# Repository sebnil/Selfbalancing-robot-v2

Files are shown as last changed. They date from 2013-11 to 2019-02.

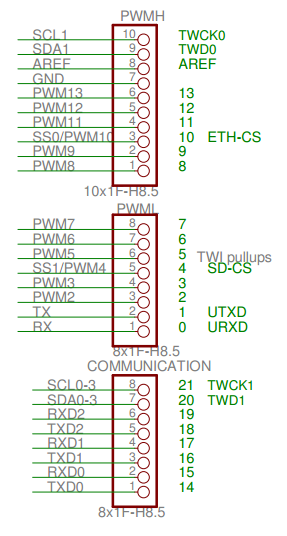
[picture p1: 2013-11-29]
schematics/Altium Designer project/arduino pins2.png

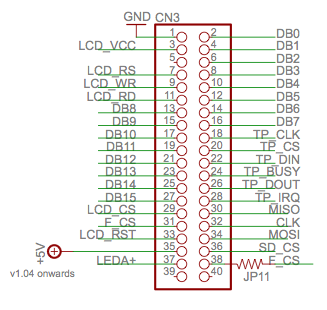
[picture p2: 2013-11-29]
schematics/Altium Designer project/lcd_pins.png

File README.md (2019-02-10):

# Selfbalancing-robot-v2

Selfbalancing robot with Arduino Due. For more details http://sebastiannilsson.com/en/k/projekt/selfbalancing-robot/

## Video
<a href="http://www.youtube.com/watch?feature=player_embedded&v=WN2oXuavrWk
" target="_blank">Selfbalancing robot</a>

## Support my creation of open source software:


<a href='https://ko-fi.com/A0A2HYRH' target='_blank'>Buy Me a Coffee at ko-fi.com</a>

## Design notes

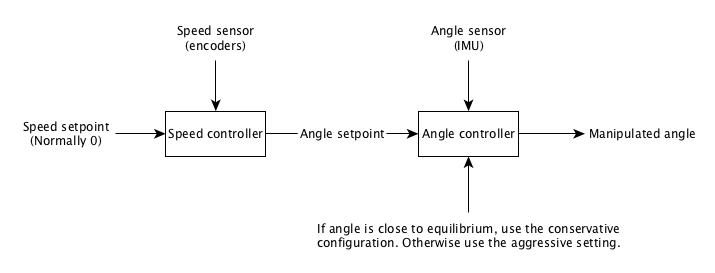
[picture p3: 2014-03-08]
Control theory/Information flow.png

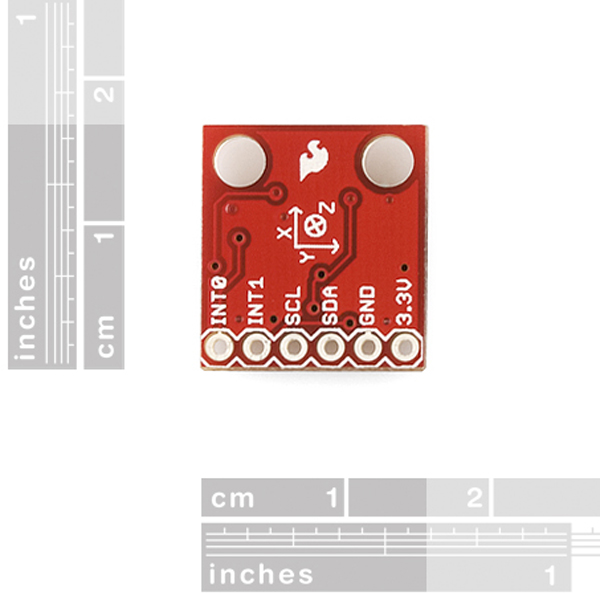
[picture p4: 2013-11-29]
schematics/Altium Designer project/sparkfun 6DOF.jpeg

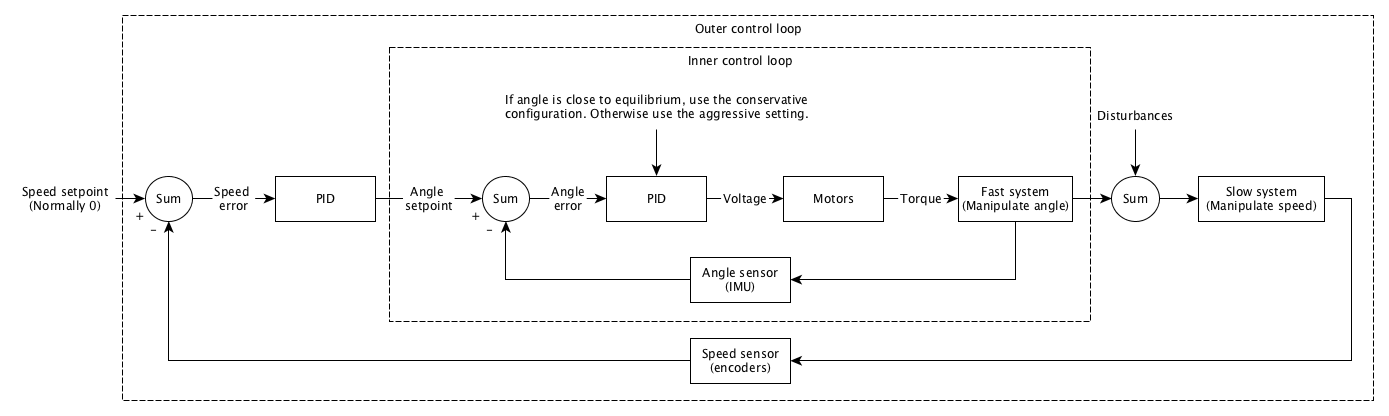
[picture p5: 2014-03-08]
Control theory/Cascade PID implementation theory.png

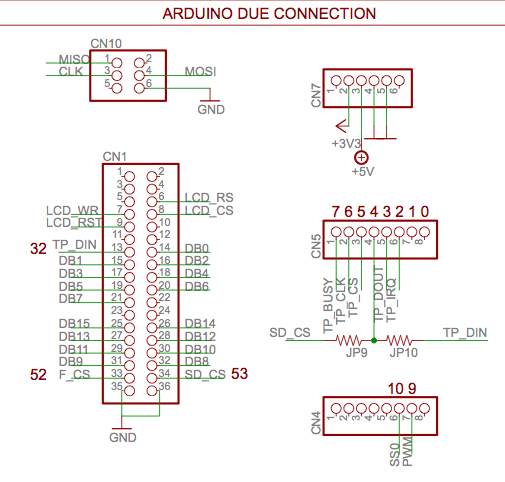
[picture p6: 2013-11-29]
schematics/Altium Designer project/lcd_arduino_connection.png

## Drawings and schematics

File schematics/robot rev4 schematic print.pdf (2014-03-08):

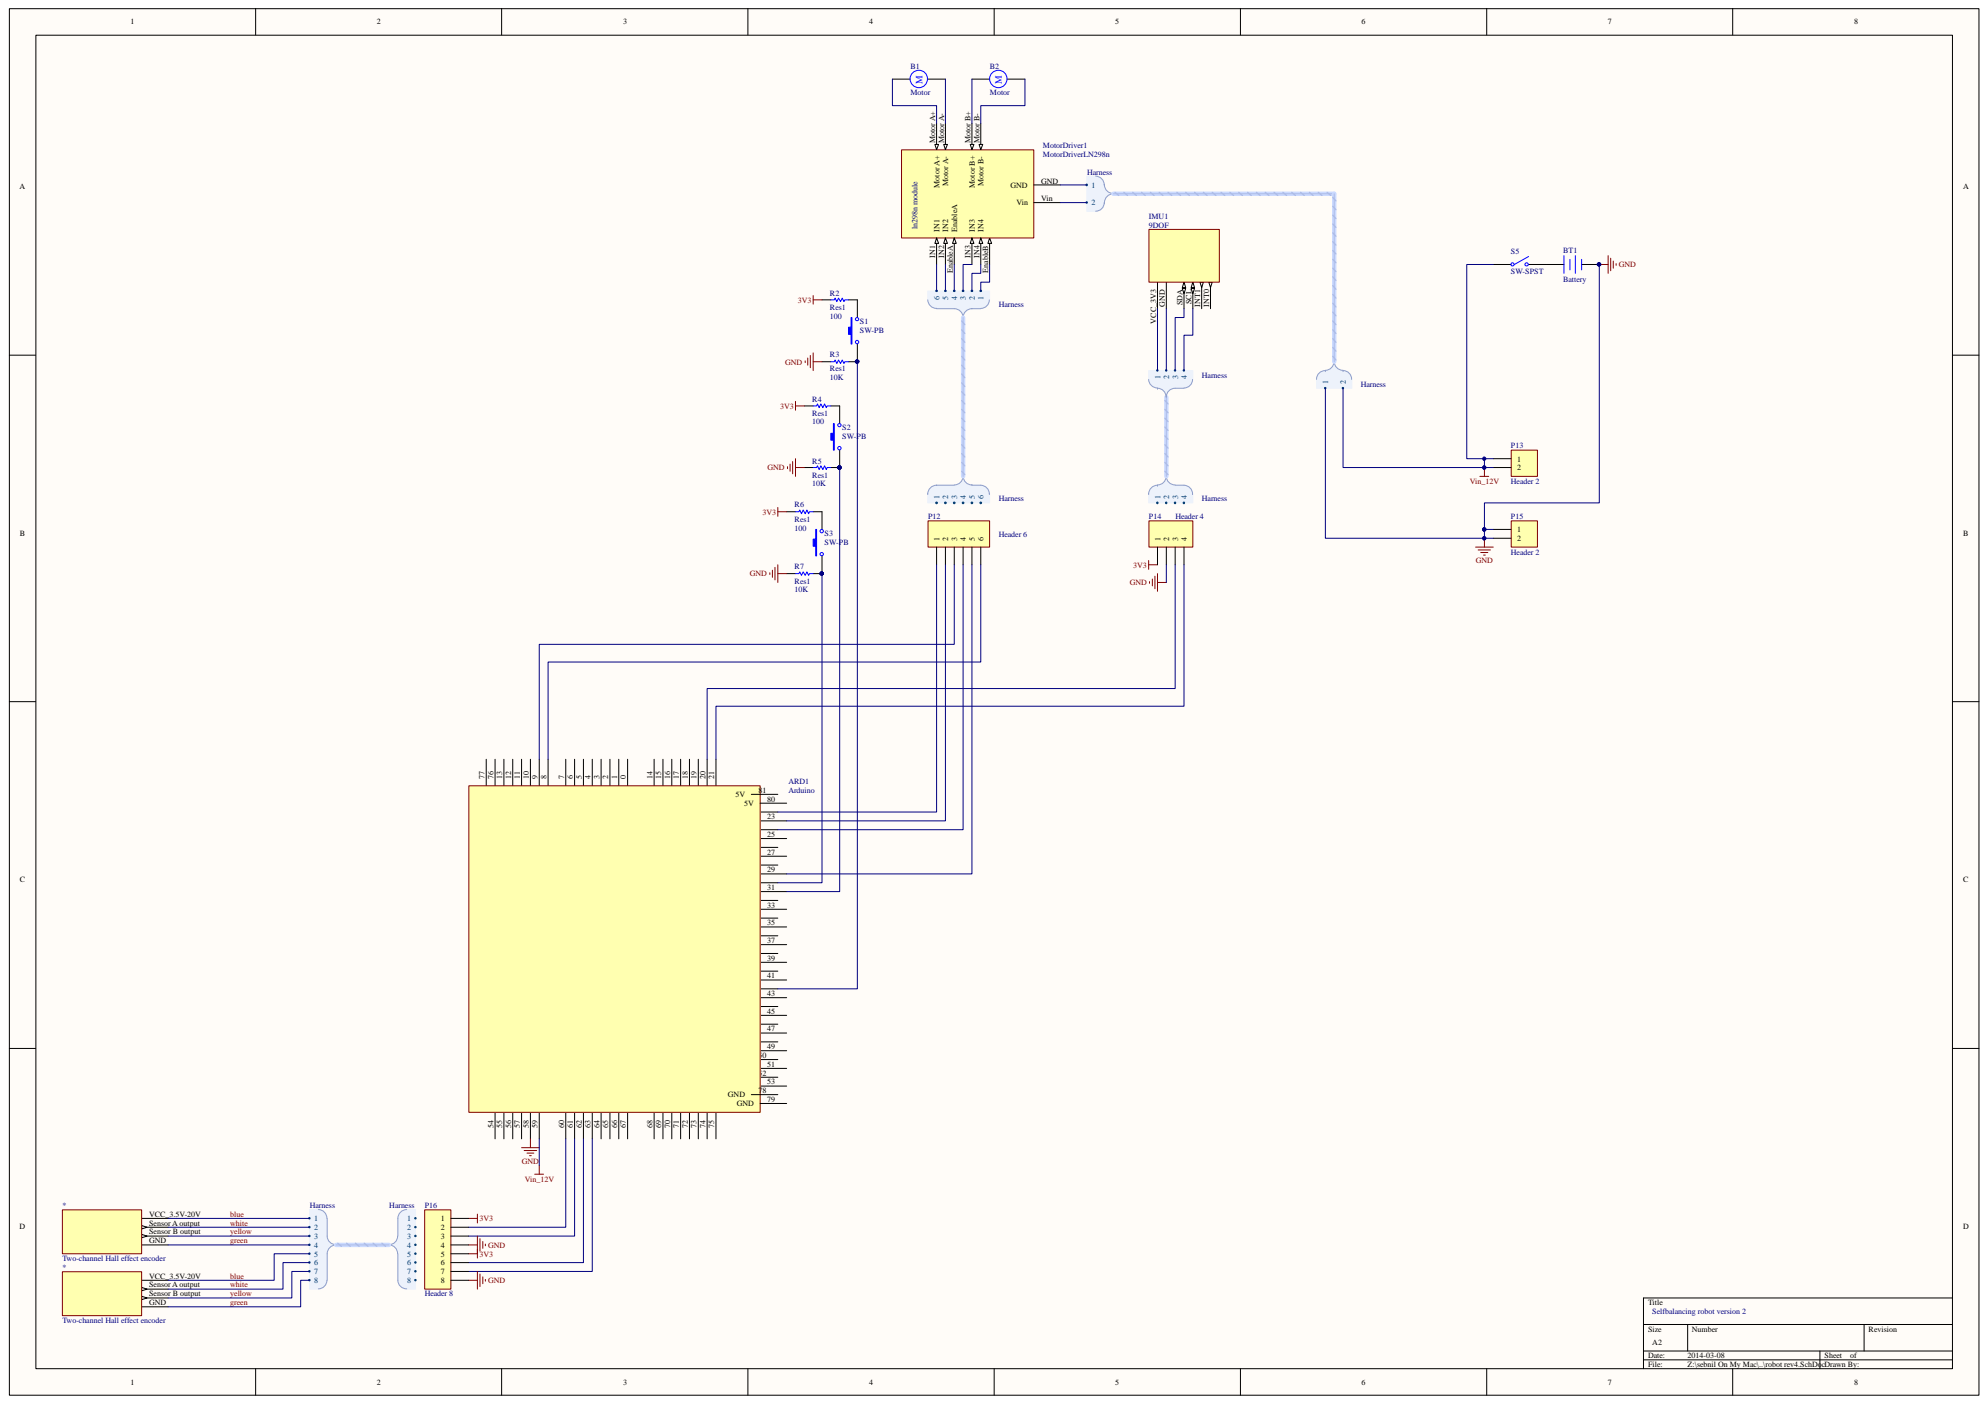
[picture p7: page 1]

Two-channel Hall effect encoder

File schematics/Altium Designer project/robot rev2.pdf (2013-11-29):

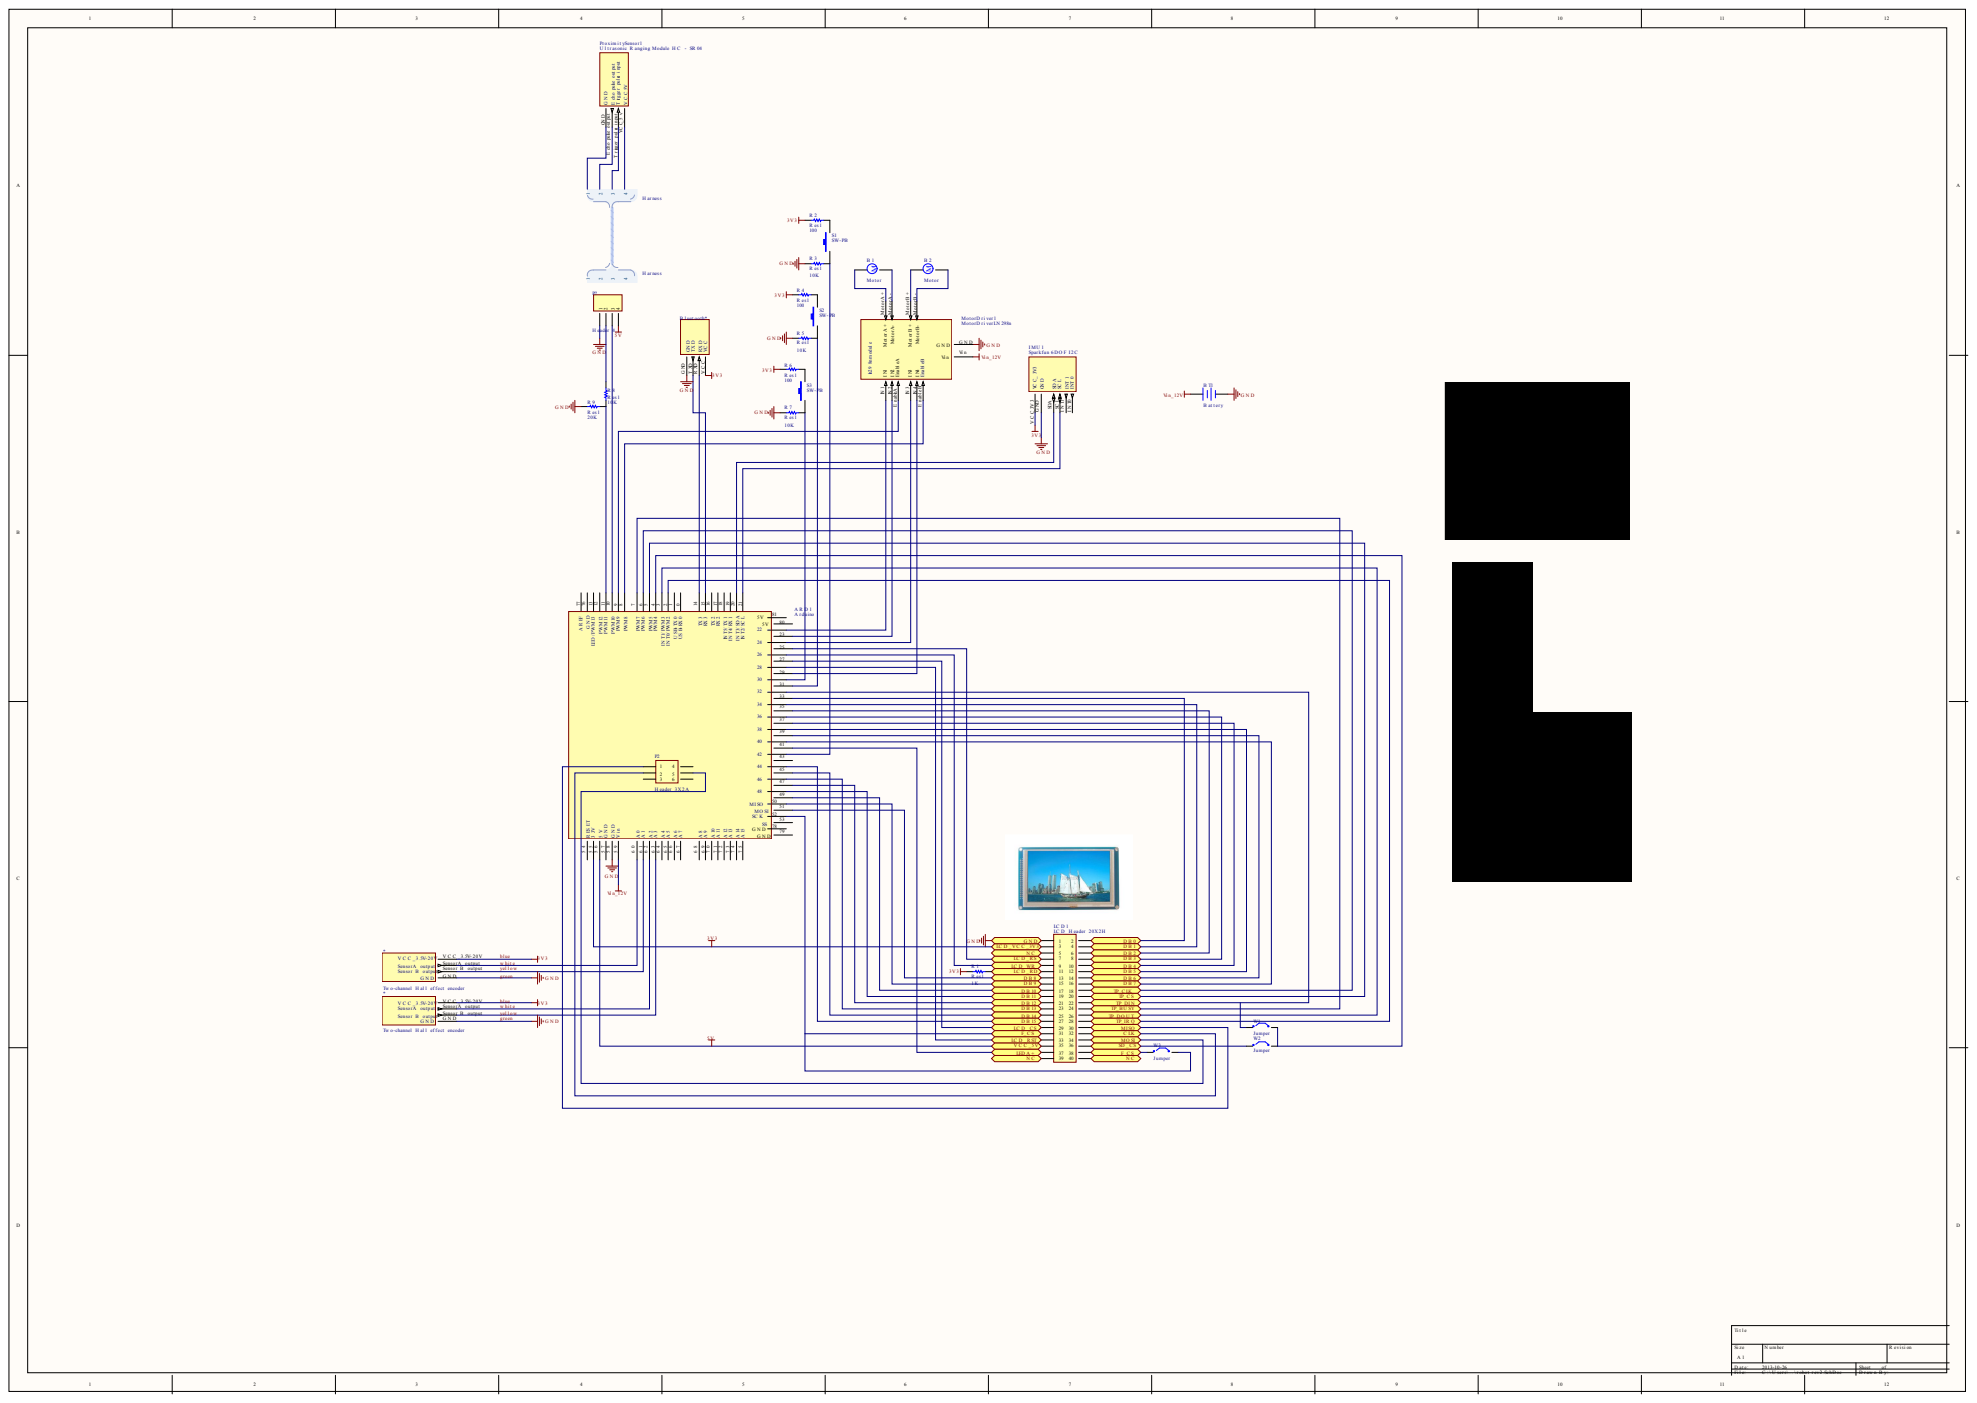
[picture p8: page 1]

Pr oxim i t ySensor1
U l t r asonic R anging Module H C - SR 04

VC C_5 v T ri gger pul se i nput T r igger pul se i nput E cho pulse out put

E cho puls e out put G N D GN D

Mot or A +

Mot or A- Mot or A -

Mot or B +

Mot or B- Mot or B -

Enabl eA E nableA I N2 IN 2

Enabl eB E nabl eB I N4 IN 4

A r duino

blue 3V3 | Vi n_12V | 3V3

SensorA output Sensor B output Sensor | SensorA output | w hit e B output yel l ow | R 1 | LC D _RS LC D _WR LC D _R D | 7 9 11 12 10 | 8 D B 3 D B 4 D B 5

Tw o-channel H al l ef f ect encoder

green blue | 3V3 | R es1 3V3 1K | D B 8 D B 9 | 13 14 15 16 | D B 6 D B 7

LC D _RST | 33 34 | MO SI

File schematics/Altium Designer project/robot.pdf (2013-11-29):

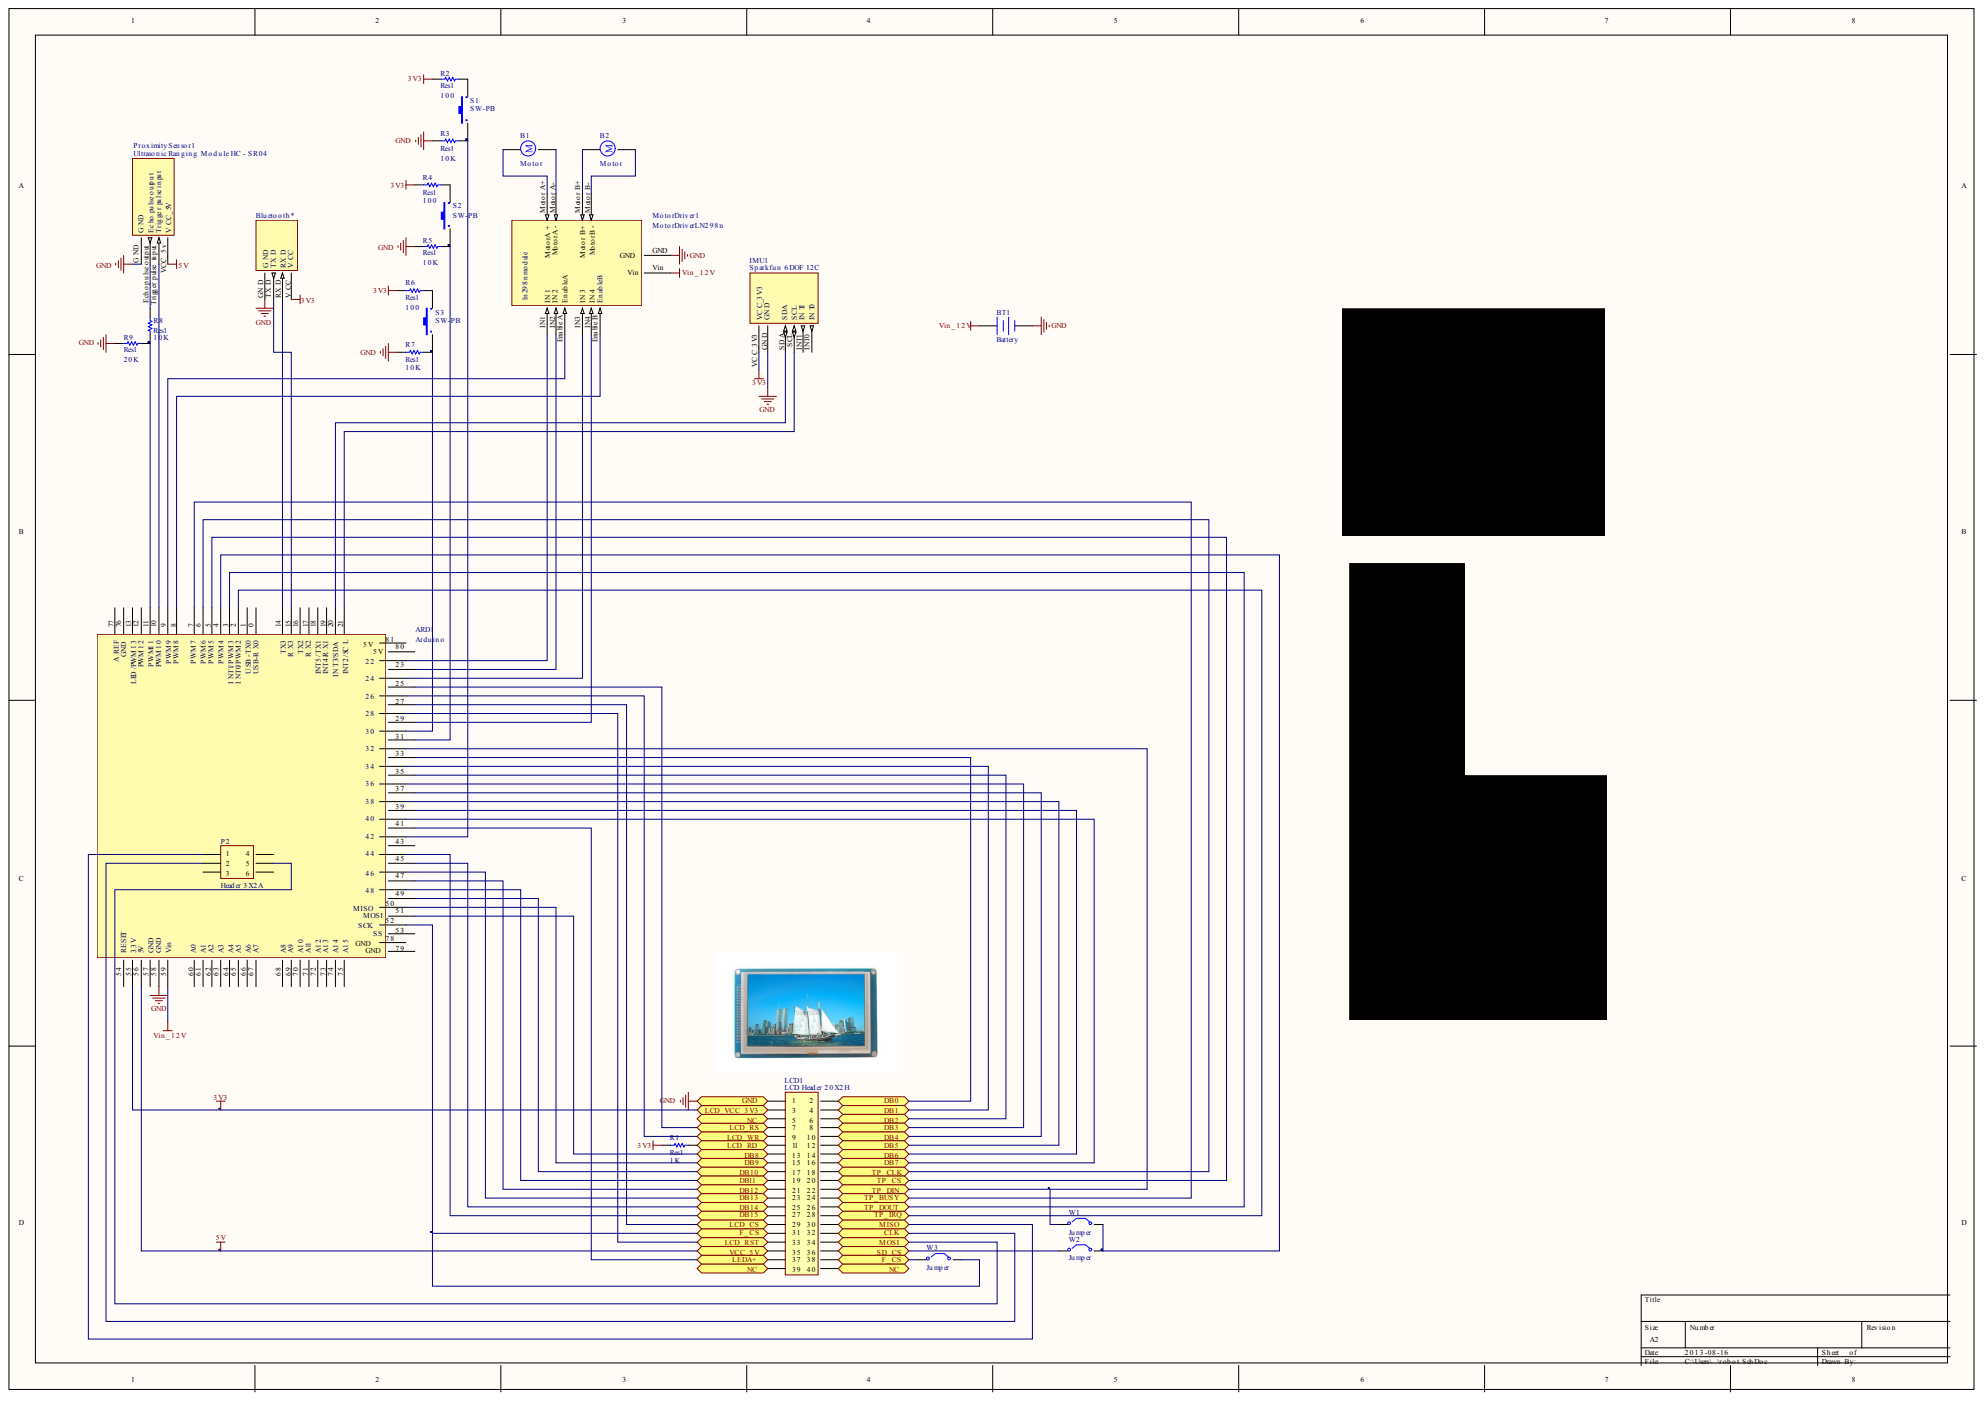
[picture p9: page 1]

V CC_ 5V VCC_ 5 v Trig ge r pu lse in pu t Trigg er p ulse in p ut Ec ho pu lse o u tp u t Ech o p u lse o utp ut G ND G ND Prox imity Sen so r1 Ultraso n ic Ran g in g Mo d u le HC - SR04

Mo to rA - Moto r A- Moto rA + Moto r A+

Mo to rB - Moto r B- Moto r B+ Moto r B+

En ab leA Ena ble A IN 2 IN2 IN 1 IN1

En ab leB Ena ble B IN 4 IN4 IN 3 IN3

IN T0 INT0 IN T1 INT1 SCL SCL SDA SD A

Res1 1 0 K

LCD_ VCC_3 V3 | 3 4

NC | 5 6 | DB2
LCD_RS | 7 8

3 V3 Res1 | DB8

R1 | LCD_ WR LCD_RD | 9 1 0 11 1 2

DB10 DB11 | 1 7 1 8 1 9 2 0 | TP_CLK TP_CS

DB12 DB13 | 2 1 2 2 2 3 2 4 | TP_ DIN TP_BUSY

DB14 | 2 5 2 6 | TP_ DOUT
DB15 | 2 7 2 8 | | W1

LCD_CS F_CS | 2 9 3 0 3 1 3 2

LCD_RST | 3 3 3 4 | MOSI W3

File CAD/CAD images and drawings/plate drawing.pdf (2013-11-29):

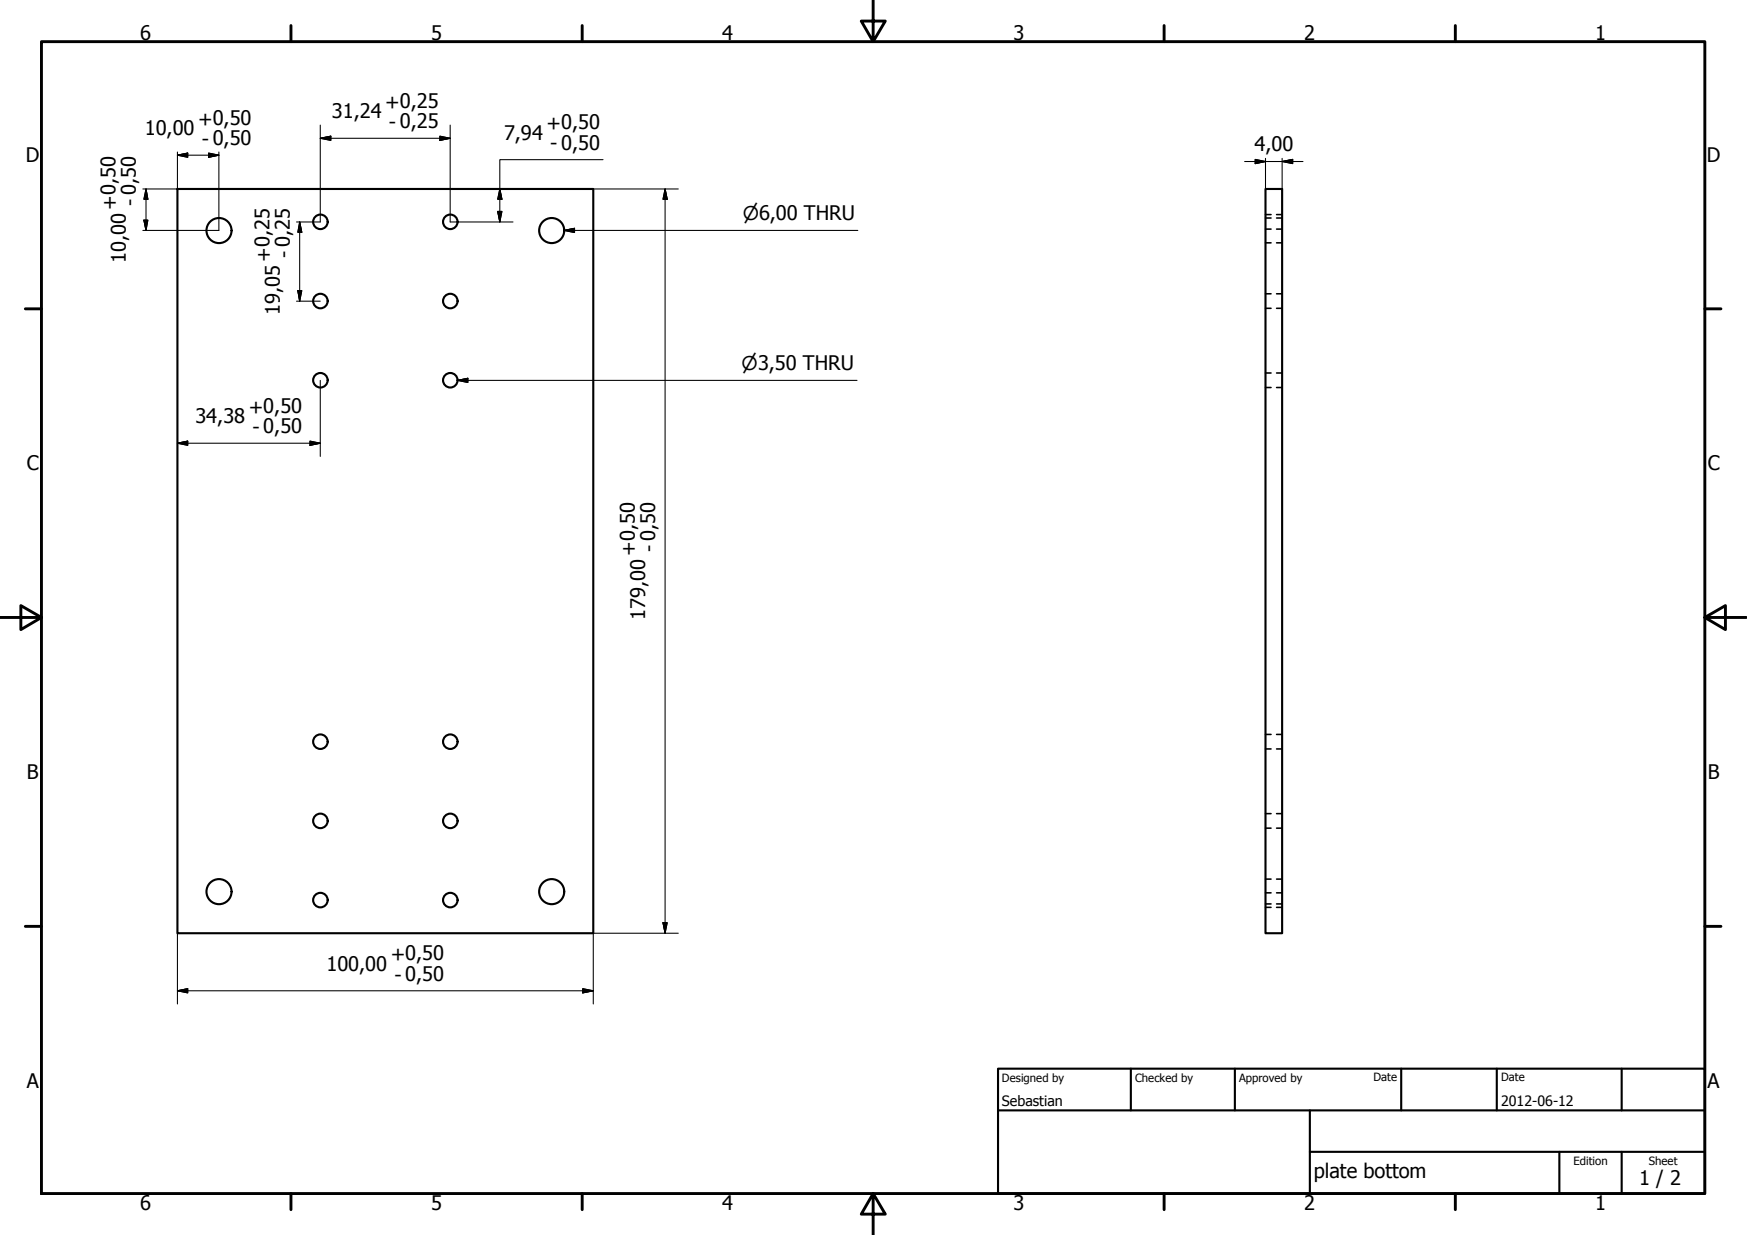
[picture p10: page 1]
plate bottom; Sebastian; Designed by; Checked by; Approved by; Date; Edition; Sheet; P3,50 THRU; P6,00 THRU

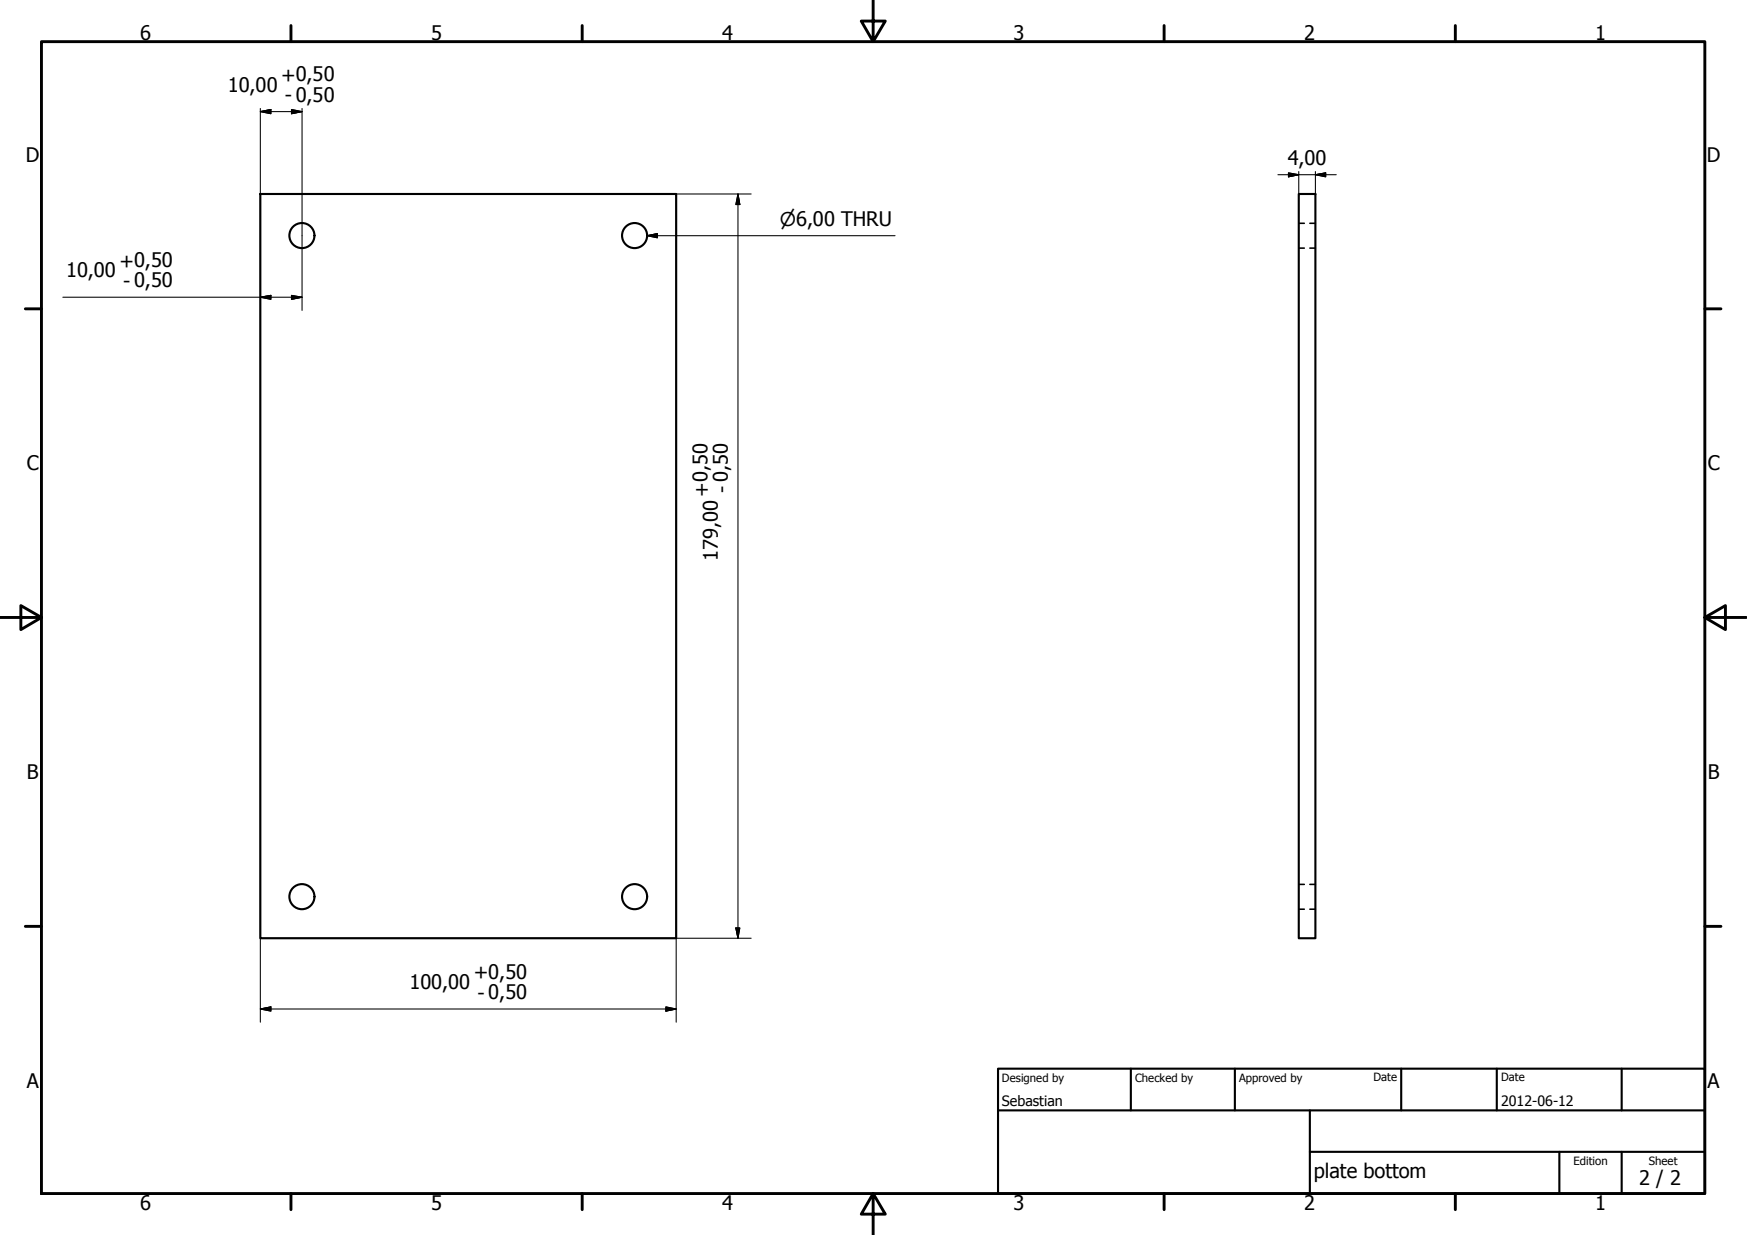
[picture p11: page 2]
plate bottom; Sebastian; Designed by; Checked by; Approved by; Date; Edition; Sheet; P6,00 THRU

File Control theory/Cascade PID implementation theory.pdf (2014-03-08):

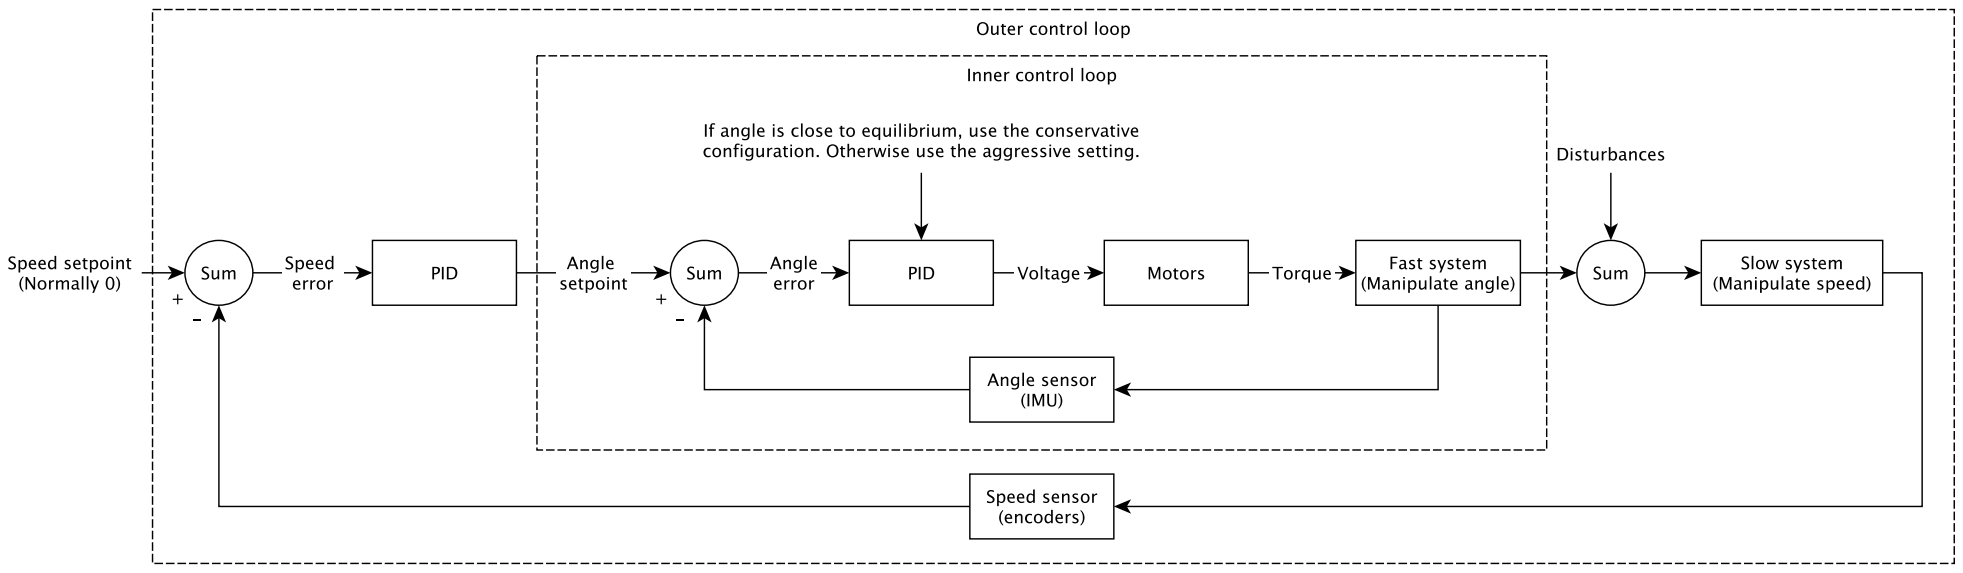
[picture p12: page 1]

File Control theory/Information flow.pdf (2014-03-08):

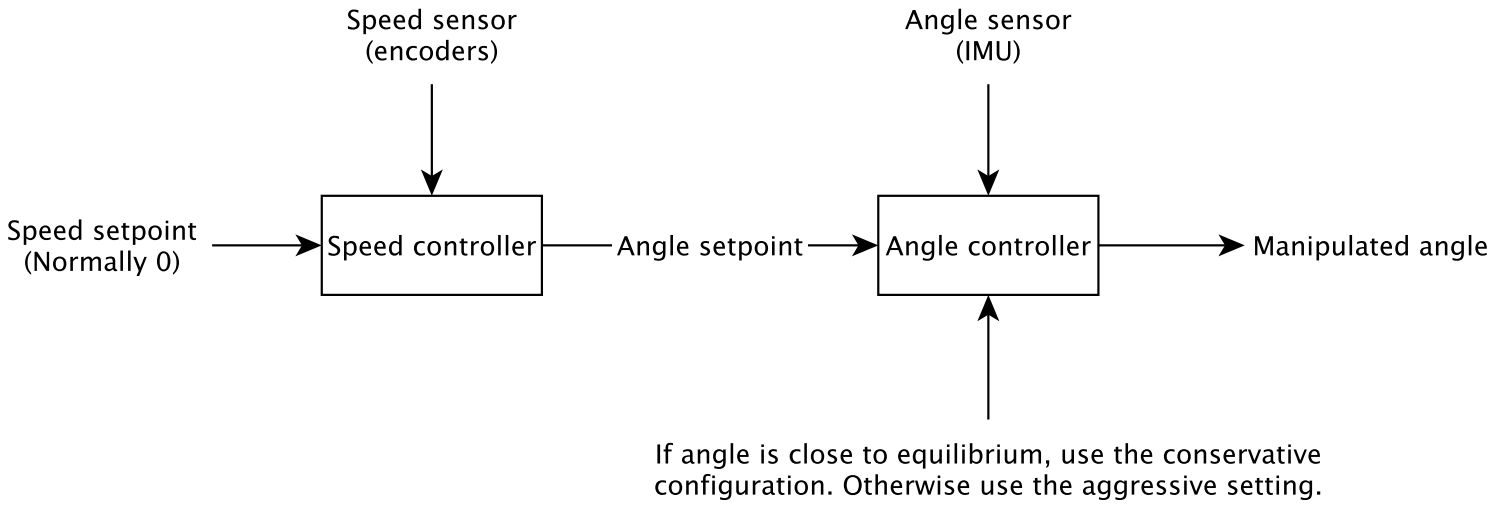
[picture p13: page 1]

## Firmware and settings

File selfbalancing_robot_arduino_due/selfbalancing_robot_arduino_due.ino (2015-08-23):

#include <Wire.h>
#include <stdlib.h>
#include <L29x.h> //https://github.com/sebnil/L29x
#include <PID_v1.h> //github.com/mwoodward/Arduino-PID-Library
#include <Button.h>        //github.com/JChristensen/Button
#include <SerialCommand.h> //github.com/kroimon/Arduino-SerialCommand
#include <MovingAvarageFilter.h> //github.com/sebnil/Moving-Avarage-Filter--Arduino-Library-
//#include <FIR.h> // github.com/sebnil/FIR-filter-Arduino-Library
#include <FIR_v2.h> // https://github.com/sebnil/FIR_v2
#include <KalmanFilter.h> // https://github.com/sebnil/KalmanFilter-for-Arduino
#include <FreeRTOS_ARM.h> //https://github.com/greiman/FreeRTOS-Arduino
#include <DueFlashStorage.h> //https://github.com/sebnil/DueFlashStorage

DueFlashStorage dueFlashStorage;


// Redefine AVR Flash string macro as nop for ARM
#undef F
#define F(str) str

#define TO_RAD(x) (x * 0.01745329252)  // *pi/180
#define TO_DEG(x) (x * 57.2957795131)  // *180/pi

const uint8_t LED_PIN = 13;

// motor config
#include <L29x.h>
L29x motorLeft(9, 22, 23); // enable (PWM), motor pin 1, motor pin 2
L29x motorRight(8, 24, 29); // enable (PWM), motor pin 1, motor pin 2

// button declarations
Button startBtn(30, false, false, 20);
Button stopBtn(31, false, false, 20);
Button calibrateBtn(42, false, false, 20);

// start and stop
boolean started = true;

SerialCommand sCmd;     // The demo SerialCommand object

// PID variables
double anglePIDSetpoint, anglePIDInput, anglePIDOutput;
double speedPIDInput, speedPIDOutput, speedPIDSetpoint;
double anglePIDInputFiltered;

// filters
MovingAvarageFilter speedMovingAvarageFilter(14);
MovingAvarageFilter angleMovingAvarageFilter(4);
KalmanFilter speedKalmanFilter;
KalmanFilter angleKalmanFilter;
FIR_v2 speedMovingAvarageFilter2;

// The cascading PIDs. The tunings are updated from the code
PID anglePID(&anglePIDInput, &anglePIDOutput, &anglePIDSetpoint, 0, 0, 0, DIRECT);
PID speedPID(&speedPIDInput, &speedPIDOutput, &speedPIDSetpoint, 0, 0, 0, DIRECT);

// handle for blink task
//xTaskHandle blink;

//v_read_imu_task
// Euler angles
float yaw;
float pitch;
float roll;
float angleRaw;
float roll_filtered;
// DCM timing in the main loop
unsigned long timestamp;
unsigned long timestamp_old;
float G_Dt; // Integration time for DCM algorithm

long leftMotorPosition  = 0;
long rightMotorPosition  = 0;
long lastLeftMotorPosition  = 0;
long lastRightMotorPosition  = 0;
float leftMotorSpeed  = 0;
float rightMotorSpeed  = 0;
float speedKalmanFiltered = 0;
float speedFIRFiltered = 0;

struct Configuration {
	double speedPIDKp;
	double speedPIDKi;
	double speedPIDKd;
	double speedPIDOutputLowerLimit;
	double speedPIDOutputHigherLimit;
	double anglePIDAggKp;
	double anglePIDAggKi;
	double anglePIDAggKd;
	double anglePIDConKp;
	double anglePIDConKi;
	double anglePIDConKd;
	double anglePIDLowerLimit;
	double calibratedZeroAngle;
	uint8_t anglePIDSampling;
	double angleKalmanFilterR;
	uint8_t speedPIDSampling;
	uint8_t angleSensorSampling;
	uint8_t motorSpeedSensorSampling;
	double speedKalmanFilterR;
	uint8_t motorLeftMinimumSpeed;
	uint8_t motorRightMinimumSpeed;
	uint8_t debugLevel;
	uint8_t debugSampleRate;
	uint8_t speedPIDOutputDebug;
	uint8_t speedPIDInputDebug;
	uint8_t speedKalmanFilterDebug;
	uint8_t speedRawDebug;
	uint8_t speedMovingAvarageFilter2Debug;
	uint8_t anglePIDSetpointDebug;
	uint8_t anglePIDInputDebug;
	uint8_t anglePIDOutputDebug;
	uint8_t angleRawDebug;
	uint8_t  activePIDTuningDebug;
};
Configuration configuration;
byte b[sizeof(Configuration)];

struct UserControl {
	float steering;
	float direction;
};
UserControl userControl = {0, 0};


void setConfiguration() {
	/* Flash is erased every time new code is uploaded. Write the default configuration to flash if first time */
	// running for the first time?
	uint8_t codeRunningForTheFirstTime = dueFlashStorage.read(0); // flash bytes will be 255 at first run
	if (codeRunningForTheFirstTime) {
		Serial.println("codeRunningForTheFirstTime");
		/* OK first time running, set defaults */
		configuration.speedPIDKp = 0.85;
		configuration.speedPIDKi = 0.10;
		configuration.speedPIDKd = 0.00;
		configuration.speedPIDOutputLowerLimit = -10.00;
		configuration.speedPIDOutputHigherLimit = 10.00;
		configuration.anglePIDAggKp = 20.00;
		configuration.anglePIDAggKi = 0.20;
		configuration.anglePIDAggKd = 0.70;
		configuration.anglePIDConKp = 15.00;
		configuration.anglePIDConKi = 0.00;
		configuration.anglePIDConKd = 0.25;
		configuration.anglePIDLowerLimit = 5.00;
		configuration.calibratedZeroAngle = -10.87;
		configuration.anglePIDSampling = 10;
		configuration.speedPIDSampling = 15;
		configuration.angleKalmanFilterR = 10.00;
		configuration.angleSensorSampling = 5;
		configuration.motorSpeedSensorSampling = 5;
		configuration.speedKalmanFilterR = 20.00;
		configuration.motorLeftMinimumSpeed = 55;
		configuration.motorRightMinimumSpeed = 55;
		
		configuration.debugLevel = 0;
		configuration.debugSampleRate = 50;
		//  configuration.speedPIDSetpointDebug = 1;
		configuration.speedPIDOutputDebug = 1;
		configuration.speedPIDInputDebug = 1;
		configuration.speedKalmanFilterDebug = 1;
		configuration.speedRawDebug = 1;
		configuration.speedMovingAvarageFilter2Debug = 0;
		configuration.anglePIDSetpointDebug = 1;
		configuration.anglePIDInputDebug = 1;
		configuration.anglePIDOutputDebug = 1;
		configuration.angleRawDebug = 1;
		configuration.activePIDTuningDebug = 1;

		// write configuration struct to flash at address 4
		//byte b2[sizeof(Configuration)]; // create byte array to store the struct
		memcpy(b, &configuration, sizeof(Configuration)); // copy the struct to the byte array
		dueFlashStorage.write(4, b, sizeof(Configuration)); // write byte array to flash
		
		// write 0 to address 0 to indicate that it is not the first time running anymore
		dueFlashStorage.write(0, 0);
	}
	else {
		Serial.println("read configuration struct from flash");
		/* read configuration struct from flash */
		byte* b2 = (dueFlashStorage.readAddress(4)); // byte array which is read from flash at address 4
		memcpy(&configuration, b2, sizeof(Configuration)); // copy byte array to temporary struct
	}
}

void setup() {
	Serial.begin(115200);
	//  Serial3.begin(9600);
	// wait for Leonardo
	while(!Serial) {
	}
	Wire.begin();

	pinMode(A0, INPUT);
	pinMode(A1, INPUT);
	pinMode(A2, INPUT);
	pinMode(A3, INPUT);
	pinMode(30, INPUT);
	pinMode(31, INPUT);
	pinMode(42, INPUT);

	attachInterrupt(A2, A2interruptFun, RISING);
	attachInterrupt(A3, A3interruptFun, RISING);

	// filters
	speedKalmanFilter.setState(0);
	float coefficients[] = {
	1,1,1,1,1,1,1,1,1          };
	speedMovingAvarageFilter2.setCoefficients(coefficients);
	speedMovingAvarageFilter2.setNumberOfTaps(9);
	speedMovingAvarageFilter2.setGain((float) (1/9));


	setConfiguration();

	// create read imu task
	//xTaskCreate(vReadIMUTask, NULL, configMINIMAL_STACK_SIZE + 50, NULL, 1, NULL);

	// create control task
	xTaskCreate(vControlTask, NULL, configMINIMAL_STACK_SIZE + 100, NULL, 1, NULL);

	// create button task
	xTaskCreate(vInterfaceAndDebugTask,NULL, configMINIMAL_STACK_SIZE+100, NULL,1,NULL);


	// start FreeRTOS
	vTaskStartScheduler();

	// should never return
	Serial.println(F("Die"));
	while(1);
}

// WARNING idle loop has a very small stack (configMINIMAL_STACK_SIZE)
// loop must never block
volatile uint32_t count = 0;
void loop() {
	while(1) {
		// must insure increment is atomic
		// in case of context switch for print
		noInterrupts();
		count++;
		interrupts();
	}
}



void newConfig() {
	// init speed PID
	speedPIDSetpoint = 0;
	speedPID.SetOutputLimits(configuration.speedPIDOutputLowerLimit, configuration.speedPIDOutputHigherLimit);
	//anglePID.SetMode(AUTOMATIC);
	speedPID.SetSampleTime(configuration.speedPIDSampling);
	speedPID.SetTunings(configuration.speedPIDKp, configuration.speedPIDKi, configuration.speedPIDKd);

	//init angle PID
	anglePIDSetpoint = 0;
	anglePID.SetOutputLimits(-100, 100);
	//anglePID.SetMode(AUTOMATIC);
	anglePID.SetSampleTime(configuration.anglePIDSampling);
	
	angleKalmanFilter.setR(configuration.angleKalmanFilterR);
	speedKalmanFilter.setR(configuration.speedKalmanFilterR);
	
	// init motors
	motorLeft.setMinimumSpeed(configuration.motorLeftMinimumSpeed);
	motorRight.setMinimumSpeed(configuration.motorRightMinimumSpeed);
	
	// write configuration struct to flash at address 4
	//byte b2[sizeof(Configuration)]; // create byte array to store the struct
	memcpy(b, &configuration, sizeof(Configuration)); // copy the struct to the byte array
	dueFlashStorage.write(4, b, sizeof(Configuration)); // write byte array to flash
}

/* interrupt functions for counting revolutions in the encoders */
void A2interruptFun() {
	if (digitalRead(A1))
	rightMotorPosition++;
	else
	rightMotorPosition--;
}
void A3interruptFun() {
	if (digitalRead(A0))
	leftMotorPosition++;
	else
	leftMotorPosition--;
}

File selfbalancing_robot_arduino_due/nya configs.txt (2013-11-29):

speedPIDKi = 5.00;
speedPIDKd = 0.00;
anglePIDAggKp = 50.00;
anglePIDAggKi = 0.00;
anglePIDAggKd = 0.00;
anglePIDConKp = 40.00;
anglePIDConKi = 1.00;
anglePIDConKd = 0.00;
anglePIDLowerLimit = 8.00;
calibratedZeroAngle = -8.60;
anglePIDSampling = 10;
speedPIDSampling = 0;
angleSensorSampling = 10;
motorSpeedSensorSampling = 10;



2013-11-29
Configuration
configuration.speedPIDKp = 0.50;
configuration.speedPIDKi = 0.01;
configuration.speedPIDKd = 0.02;
configuration.speedPIDOutputLowerLimit = -3.00;
configuration.speedPIDOutputHigherLimit = 3.00;
configuration.anglePIDAggKp = 0.80;
configuration.anglePIDAggKi = 0.00;
configuration.anglePIDAggKd = 0.00;
configuration.anglePIDConKp = 20.00;
configuration.anglePIDConKi = 0.50;
configuration.anglePIDConKd = 0.25;
configuration.anglePIDLowerLimit = 20.00;
configuration.calibratedZeroAngle = -11.35;
configuration.anglePIDSampling = 10;
configuration.speedPIDSampling = 5;
configuration.angleSensorSampling = 10;
configuration.motorSpeedSensorSampling = 10;
configuration.debugLevel = 0;



configuration.speedPIDKp = 0.50;
configuration.speedPIDKi = 0.01;
configuration.speedPIDKd = 0.01;
configuration.speedPIDOutputLowerLimit = -3.00;
configuration.speedPIDOutputHigherLimit = 3.00;
configuration.anglePIDAggKp = 50.00;
configuration.anglePIDAggKi = 0.00;
configuration.anglePIDAggKd = 0.00;
configuration.anglePIDConKp = 20.00;
configuration.anglePIDConKi = 0.50;
configuration.anglePIDConKd = 0.25;
configuration.anglePIDLowerLimit = 5.00;
configuration.calibratedZeroAngle = -11.35;
configuration.anglePIDSampling = 10;
configuration.speedPIDSampling = 5;
configuration.angleKalmanFilterR = 1.00;
configuration.angleSensorSampling = 15;
configuration.motorSpeedSensorSampling = 10;
configuration.speedKalmanFilterR = 3.00;

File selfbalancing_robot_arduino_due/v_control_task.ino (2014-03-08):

enum PIDTuning {CONSERVATIVE, AGGRESSIVE};
PIDTuning activePIDTuning = CONSERVATIVE;

//uint32_t controlTaskTimestamp = 0;
static void vControlTask(void *pvParameters) {
	newConfig();
	
	// Init sensors
	vTaskDelay(50);  // Give sensors enough time to start
	I2C_Init();
	Accel_Init();
	Magn_Init();
	Gyro_Init();
	// Read sensors, init DCM algorithm
	vTaskDelay(20);  // Give sensors enough time to collect data
	reset_sensor_fusion();
	Serial.println("imu init done");

	for (;;) {
		// Time to read the sensors again?
		if((millis() - timestamp) >= configuration.angleSensorSampling) {
			timestamp_old = timestamp;
			timestamp = millis();
			if (timestamp > timestamp_old)
			G_Dt = (float) (timestamp - timestamp_old) / 1000.0f; // Real time of loop run. We use this on the DCM algorithm (gyro integration time)
			else G_Dt = 0;

			// Update sensor readings
			read_sensors();

			// Apply sensor calibration
			compensate_sensor_errors();

			// Run DCM algorithm
			Compass_Heading(); // Calculate magnetic heading
			Matrix_update();
			Normalize();
			Drift_correction();
			Euler_angles();

			// update speeed
			rightMotorSpeed = (float) (rightMotorPosition - lastRightMotorPosition);
			lastRightMotorPosition = rightMotorPosition;
			leftMotorSpeed = (float) (leftMotorPosition - lastLeftMotorPosition);
			lastLeftMotorPosition = leftMotorPosition;

			//speedPIDInput = (rightMotorSpeed+leftMotorSpeed);

			speedKalmanFilter.correct(rightMotorSpeed+leftMotorSpeed);
			speedKalmanFiltered = speedKalmanFilter.getState();
			speedPIDInput = speedKalmanFiltered;
			//speedFIRFiltered = speedMovingAvarageFilter2.process(rightMotorSpeed+leftMotorSpeed);
			
			
			// move angle to around equilibrium
			if (roll < 0) {
				angleRaw = (TO_DEG(roll) + 180)-configuration.calibratedZeroAngle;
			}
			else {
				angleRaw =(TO_DEG(roll) - 180)-configuration.calibratedZeroAngle;
			}
			if (true)  {
				angleKalmanFilter.correct(angleRaw);
				anglePIDInput = angleKalmanFilter.getState();
			}
			else {
				anglePIDInput = angleRaw;
			}
		}

		// Time again?
		/*if((millis() - controlTaskTimestamp) >= 10) {
		controlTaskTimestamp = millis();*/
		
		speedPIDSetpoint = userControl.direction;

		// speed pid. input is wheel speed. output is angleSetpoint
		speedPID.Compute();
		anglePIDSetpoint = -speedPIDOutput;

		// update angle pid tuning. only update if different from current tuning
		if((activePIDTuning == AGGRESSIVE) && (abs(anglePIDInput) < configuration.anglePIDLowerLimit)) {
			//we're close to setpoint, use conservative tuning parameters
			activePIDTuning = CONSERVATIVE;
			anglePID.SetTunings(configuration.anglePIDConKp, configuration.anglePIDConKi, configuration.anglePIDConKd);
		}
		else if ((activePIDTuning == CONSERVATIVE) && (abs(anglePIDInput) >= configuration.anglePIDLowerLimit)) {
			//we're far from setpoint, use aggressive tuning parameters
			activePIDTuning = AGGRESSIVE;
			anglePID.SetTunings(configuration.anglePIDAggKp, configuration.anglePIDAggKi, configuration.anglePIDAggKd);
		}
		else if (abs(anglePIDInput) > 30){
			// fell down
			started = false;
		}
		anglePID.Compute();
		if (started) {
			if (userControl.steering > 0) {
				motorLeft.setSpeedPercentage(anglePIDOutput+userControl.steering);
				motorRight.setSpeedPercentage(anglePIDOutput);
			}
			else if (userControl.steering < 0) {
				motorLeft.setSpeedPercentage(anglePIDOutput);
				motorRight.setSpeedPercentage(anglePIDOutput-userControl.steering);
			}
			else {
				motorLeft.setSpeedPercentage(anglePIDOutput);
				motorRight.setSpeedPercentage(anglePIDOutput);
			}
		}
		else {
			motorLeft.setSpeed(0);
			motorRight.setSpeed(0);
		}
		//}
	}
}

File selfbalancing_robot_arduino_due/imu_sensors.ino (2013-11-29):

/* This file is part of the Razor AHRS Firmware */

// I2C code to read the sensors

// Sensor I2C addresses
#define ACCEL_ADDRESS ((int16_t) 0x53) // 0x53 = 0xA6 / 2
#define MAGN_ADDRESS  ((int16_t) 0x1E) // 0x1E = 0x3C / 2
#define GYRO_ADDRESS  ((int16_t) 0x68) // 0x68 = 0xD0 / 2

// Arduino backward compatibility macros
#if ARDUINO >= 100
#define WIRE_SEND(b) Wire.write((byte) b)
#define WIRE_RECEIVE() Wire.read()
#else
#define WIRE_SEND(b) Wire.send(b)
#define WIRE_RECEIVE() Wire.receive()
#endif


void I2C_Init()
{
	Wire.begin();
}

void Accel_Init()
{
	Wire.beginTransmission(ACCEL_ADDRESS);
	WIRE_SEND(0x2D);  // Power register
	WIRE_SEND(0x08);  // Measurement mode
	Wire.endTransmission();
	delay(5);
	Wire.beginTransmission(ACCEL_ADDRESS);
	WIRE_SEND(0x31);  // Data format register
	WIRE_SEND(0x08);  // Set to full resolution
	Wire.endTransmission();
	delay(5);
	
	// Because our main loop runs at 50Hz we adjust the output data rate to 50Hz (25Hz bandwidth)
	Wire.beginTransmission(ACCEL_ADDRESS);
	WIRE_SEND(0x2C);  // Rate
	WIRE_SEND(0x09);  // Set to 50Hz, normal operation
	Wire.endTransmission();
	delay(5);
}

// Reads x, y and z accelerometer registers
void Read_Accel()
{
	int16_t i = 0;
	byte buff[6];
	
	Wire.beginTransmission(ACCEL_ADDRESS);
	WIRE_SEND(0x32);  // Send address to read from
	Wire.endTransmission();
	
	Wire.beginTransmission(ACCEL_ADDRESS);
	Wire.requestFrom(ACCEL_ADDRESS, 6);  // Request 6 bytes
	while(Wire.available())  // ((Wire.available())&&(i<6))
	{
		buff[i] = WIRE_RECEIVE();  // Read one byte
		i++;
	}
	Wire.endTransmission();
	
	if (i == 6)  // All bytes received?
	{
		// No multiply by -1 for coordinate system transformation here, because of double negation:
		// We want the gravity vector, which is negated acceleration vector.
		accel[0] = (int16_t) ((( buff[3]) << 8) | buff[2]);  // X axis (internal sensor y axis)
		accel[1] = (int16_t) ((( buff[1]) << 8) | buff[0]);  // Y axis (internal sensor x axis)
		accel[2] = (int16_t) ((( buff[5]) << 8) | buff[4]);  // Z axis (internal sensor z axis)
	}
	else
	{
		num_accel_errors++;
		if (output_errors) Serial.println("!ERR: reading accelerometer");
	}
}

void Magn_Init()
{
	Wire.beginTransmission(MAGN_ADDRESS);
	WIRE_SEND(0x02);
	WIRE_SEND(0x00);  // Set continuous mode (default 10Hz)
	Wire.endTransmission();
	delay(5);

	Wire.beginTransmission(MAGN_ADDRESS);
	WIRE_SEND(0x00);
	WIRE_SEND(0b00011000);  // Set 50Hz
	Wire.endTransmission();
	delay(5);
}

void Read_Magn()
{
	int16_t i = 0;
	byte buff[6];
	
	Wire.beginTransmission(MAGN_ADDRESS);
	WIRE_SEND(0x03);  // Send address to read from
	Wire.endTransmission();
	
	Wire.beginTransmission(MAGN_ADDRESS);
	Wire.requestFrom(MAGN_ADDRESS, 6);  // Request 6 bytes
	while(Wire.available())  // ((Wire.available())&&(i<6))
	{
		buff[i] = WIRE_RECEIVE();  // Read one byte
		i++;
	}
	Wire.endTransmission();
	
	if (i == 6)  // All bytes received?
	{
		// 9DOF Razor IMU SEN-10125 using HMC5843 magnetometer
		#if HW__VERSION_CODE == 10125
		// MSB byte first, then LSB; X, Y, Z
		magnetom[0] = -1 * (int16_t) ((( buff[2]) << 8) | buff[3]);  // X axis (internal sensor -y axis)
		magnetom[1] = -1 * (int16_t) ((( buff[0]) << 8) | buff[1]);  // Y axis (internal sensor -x axis)
		magnetom[2] = -1 * (int16_t) ((( buff[4]) << 8) | buff[5]);  // Z axis (internal sensor -z axis)
		// 9DOF Razor IMU SEN-10736 using HMC5883L magnetometer
		#elif HW__VERSION_CODE == 10736
		// MSB byte first, then LSB; Y and Z reversed: X, Z, Y
		magnetom[0] = -1 * (int16_t) ((( buff[4]) << 8) | buff[5]);  // X axis (internal sensor -y axis)
		magnetom[1] = -1 * (int16_t) ((( buff[0]) << 8) | buff[1]);  // Y axis (internal sensor -x axis)
		magnetom[2] = -1 * (int16_t) ((( buff[2]) << 8) | buff[3]);  // Z axis (internal sensor -z axis)
		// 9DOF Sensor Stick SEN-10183 and SEN-10321 using HMC5843 magnetometer
		#elif (HW__VERSION_CODE == 10183) || (HW__VERSION_CODE == 10321)
		// MSB byte first, then LSB; X, Y, Z
		magnetom[0] = (int16_t) ((( buff[0]) << 8) | buff[1]);         // X axis (internal sensor x axis)
		magnetom[1] = -1 * (int16_t) ((( buff[2]) << 8) | buff[3]));  // Y axis (internal sensor -y axis)
		magnetom[2] = -1 * (int16_t) ((( buff[4]) << 8) | buff[5]));  // Z axis (internal sensor -z axis)
		// 9DOF Sensor Stick SEN-10724 using HMC5883L magnetometer
		#elif HW__VERSION_CODE == 10724
		// MSB byte first, then LSB; Y and Z reversed: X, Z, Y
		magnetom[0] = (int16_t) (( buff[0]) << 8) | buff[1]);         // X axis (internal sensor x axis)
		magnetom[1] = -1 * (int16_t) ((( buff[4]) << 8) | buff[5]);  // Y axis (internal sensor -y axis)
		magnetom[2] = -1 * (int16_t) ((( buff[2]) << 8) | buff[3]);  // Z axis (internal sensor -z axis)
		#endif
	}
	else
	{
		num_magn_errors++;
		if (output_errors) Serial.println("!ERR: reading magnetometer");
	}
}

void Gyro_Init()
{
	// Power up reset defaults
	Wire.beginTransmission(GYRO_ADDRESS);
	WIRE_SEND(0x3E);
	WIRE_SEND(0x80);
	Wire.endTransmission();
	delay(5);
	
	// Select full-scale range of the gyro sensors
	// Set LP filter bandwidth to 42Hz
	Wire.beginTransmission(GYRO_ADDRESS);
	WIRE_SEND(0x16);
	WIRE_SEND(0x1B);  // DLPF_CFG = 3, FS_SEL = 3
	Wire.endTransmission();
	delay(5);
	
	// Set sample rato to 50Hz
	Wire.beginTransmission(GYRO_ADDRESS);
	WIRE_SEND(0x15);
	WIRE_SEND(0x0A);  //  SMPLRT_DIV = 10 (50Hz)
	Wire.endTransmission();
	delay(5);

	// Set clock to PLL with z gyro reference
	Wire.beginTransmission(GYRO_ADDRESS);
	WIRE_SEND(0x3E);
	WIRE_SEND(0x00);
	Wire.endTransmission();
	delay(5);
}

// Reads x, y and z gyroscope registers
void Read_Gyro()
{
	int16_t i = 0;
	byte buff[6];
	
	Wire.beginTransmission(GYRO_ADDRESS);
	WIRE_SEND(0x1D);  // Sends address to read from
	Wire.endTransmission();
	
	Wire.beginTransmission(GYRO_ADDRESS);
	Wire.requestFrom(GYRO_ADDRESS, 6);  // Request 6 bytes
	while(Wire.available())  // ((Wire.available())&&(i<6))
	{
		buff[i] = WIRE_RECEIVE();  // Read one byte
		i++;
	}
	Wire.endTransmission();
	
	if (i == 6)  // All bytes received?
	{
		gyro[0] = -1 * (int16_t) ((( buff[2]) << 8) | buff[3]);    // X axis (internal sensor -y axis)
		gyro[1] = -1 * (int16_t) ((( buff[0]) << 8) | buff[1]);    // Y axis (internal sensor -x axis)
		gyro[2] = -1 * (int16_t) ((( buff[4]) << 8) | buff[5]);    // Z axis (internal sensor -z axis)
	}
	else
	{
		num_gyro_errors++;
		if (output_errors) Serial.println("!ERR: reading gyroscope");
	}
}

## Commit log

2013-11-29 Adding CAD, BOM, schematics and Atmel Studio project
    [LCD.SchDoc, Self balancing robot rev2.PrjPcb, Self balancing robot rev3.PrjPcb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]
2014-03-08 Added schematics and did some cleanup
    [robot rev4.SchDoc]
2015-08-23 Fixing references to libraries.
    [selfbalancing_robot_arduino_due.ino]
